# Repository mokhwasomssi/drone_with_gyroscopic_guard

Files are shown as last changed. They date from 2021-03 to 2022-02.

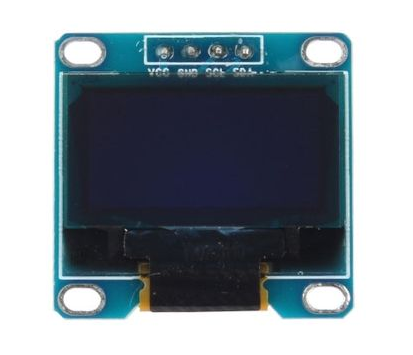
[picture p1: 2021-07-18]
reference/display/SSD1306 I2C Module 3.png

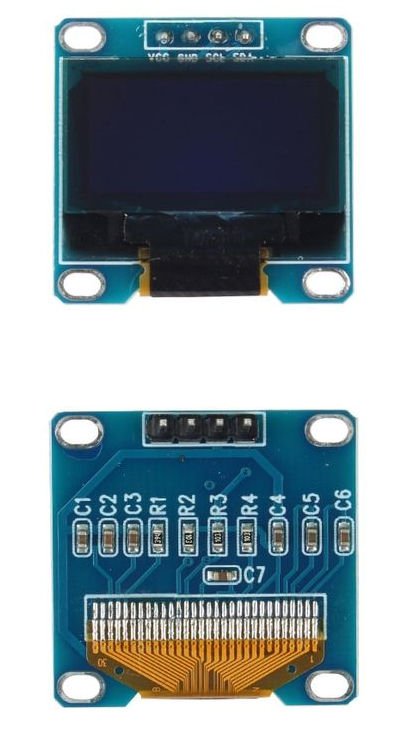
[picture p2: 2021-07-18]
reference/display/SSD1306 I2C Module 1.png

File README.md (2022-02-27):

# drone with gyroscopic guard

**Develop drone firmware and Design gyroscopic guard**



---

## Dev Environment
### Tools
- STM32CubeIDE
- Solidworks
- Kicad
 
---
## System Architecture

drone with my controller

---

## Parts

### 1. Gyroscopic Guard



#### Configuration

- 3mm carbon rod
- 3mm carbon plate
- Small bearing
- Shaft
- 3d printed parts

#### Feature

- Protect drones and Respond flexibly to collisions.
- x-axis drone mounter
- x-axis gyroscope ring
- y-axis gyroscope ring
- z-axis 2V geodesic sphere

### 2. Quadcopter



#### Configuration

- STM32F4CEU6 core board
- 210mm frame  
- 2207 2450KV BLDC  
- 5045 props  
- 3S-4S PDB  
- BLHeli_32 35A ESC  
- IMU (ICM20948)
- RF Transceiver (nrf24l01+pa+lna)
- Buzzer  
- 4S Lipo Battery  
- Battery Monitor Circuit
- SWD (st-link)  

#### Schematic



#### Feature

- 1 Khz PID loop
- Battery Monitor
- [ICM20948 library](https://github.com/mokhwasomssi/stm32_hal_icm20948.git)
- [Dshot protocol library](https://github.com/mokhwasomssi/stm32_hal_dshot.git)

### 3. Controller



#### Configuration

- STM32F4CEU6 core board
- Joy Stick X 2
- OLED LCD
- RF Transceiver (nrf24l01+pa+lna)
- Switch X 2 (with led)
- Buzzer
- 18650 battery X 2

#### Schematic


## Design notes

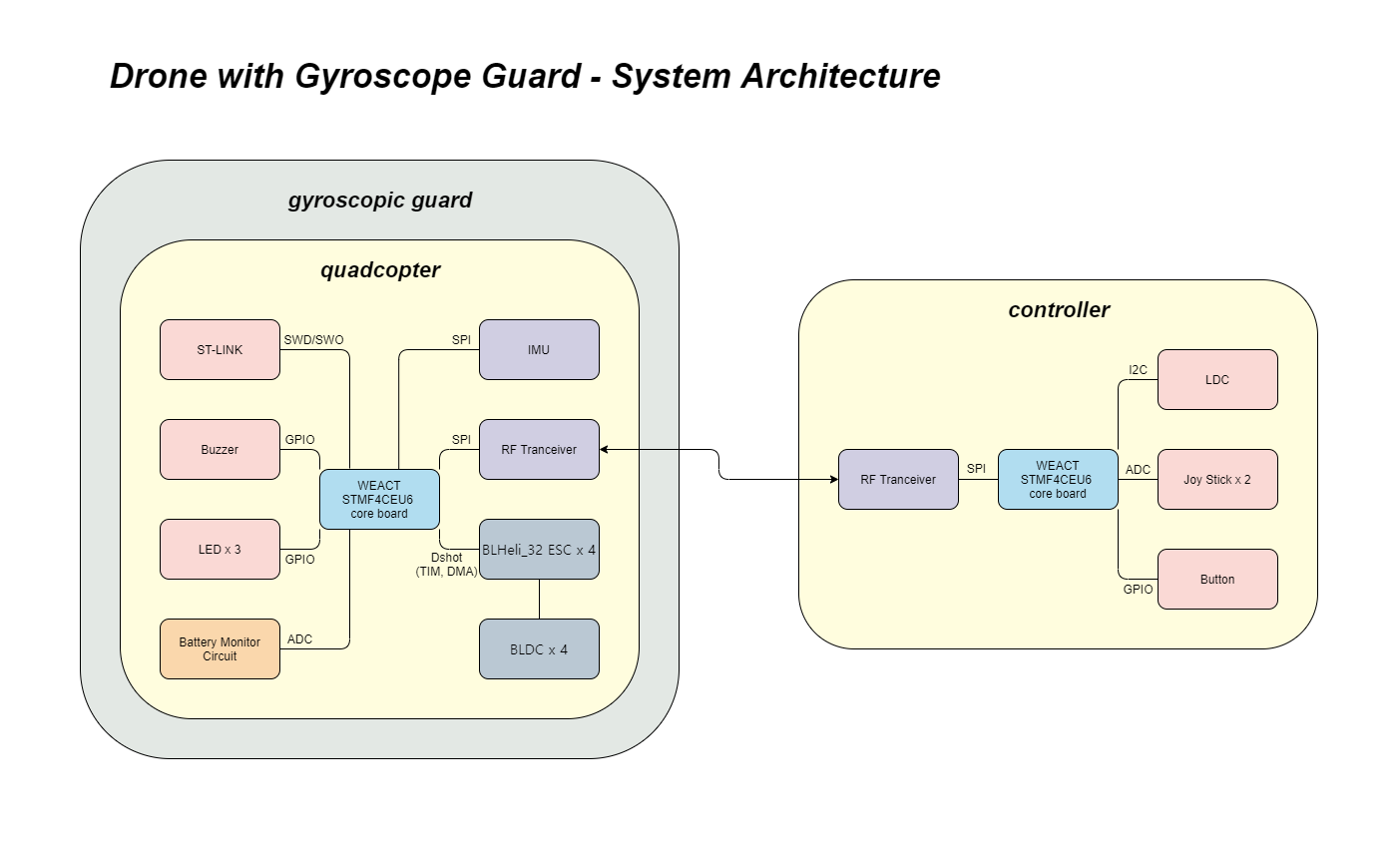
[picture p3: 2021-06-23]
docs/System Architecture.png

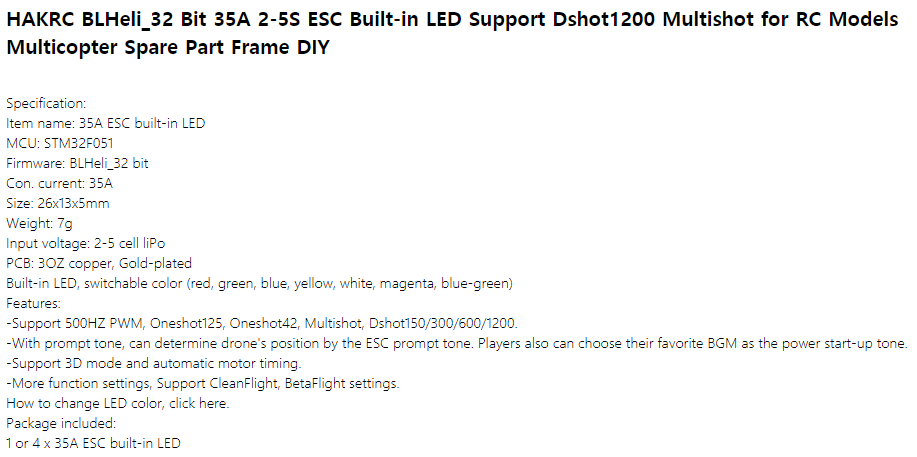
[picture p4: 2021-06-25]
reference/esc/HAKRC BLHeli_32 35A ESC Spec.png

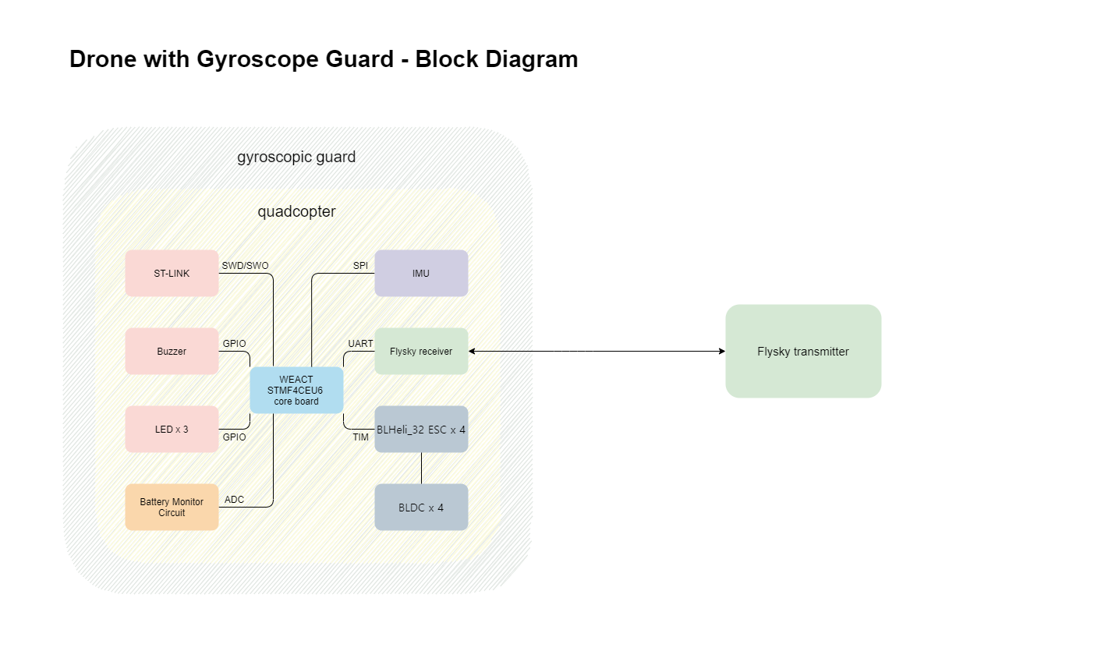
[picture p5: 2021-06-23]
docs/drone with flysky controller.png

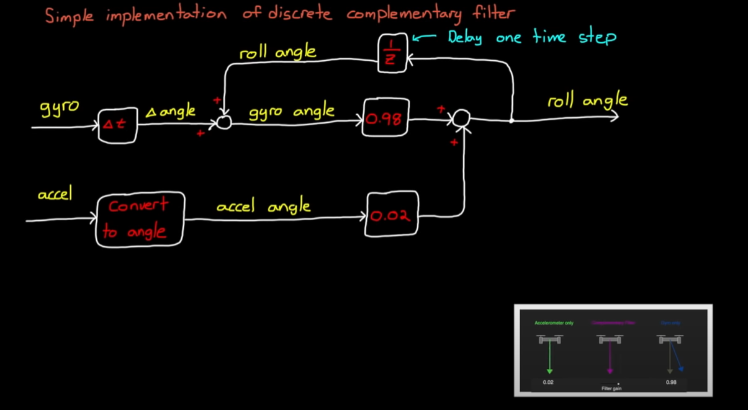
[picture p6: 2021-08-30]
document/complementary filter.png

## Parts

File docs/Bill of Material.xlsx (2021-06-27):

quadcopter |  |  | controller
 | 품명 | 구매처
1 | WeAct Black Pill V3.0 (STM32F411CEU6) |  | 1 | WeAct Black Pill V3.0 (STM32F411CEU6)
2 | SparkFun 9Dof IMU Breakout - ICM-20948 (Qwiic) |  | 2 | nrf24l01+pa+lna rf transceiver module
3 | nrf24l01+pa+lna rf transceiver module |  | 3 | SSD1306 OLED 128x64 0.96inch I2C
4 | Matek PDB-XT60 3-4S |  | 4 | joystick |  | 14.8 | 16.8 | diff
5 | HAKRC BLHeli_32 Bit 35A 2-5S ESC |  | 5 |  | 1 | 14.8 | 16.8 | 2
6 | lm358n |  | 6 |  | 2 | 7.4 | 8.4 | 1
7 | ZOP Power 14.8V 1800mAh 65C 4S Lipo Battery XT60 Plug | 뱅굿 (https://www.banggood.com/ZOP-Power-14_8V-1800mAh-65C-4S-Lipo-Battery-XT60-Plug-For-RC-FPV-Racing-Drone-p-1089557.html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) | 7 |  | 3 | 4.933333333 | 5.6 | 0.6666666667
8 | iFlight XING E 2207 2450KV |  | 8 |  | 4 | 3.7 | 4.2 | 0.5
9 |  |  | 9 |  | 5 | 2.96 | 3.36 | 0.4
 |  |  | 10 |  | 6 | 2.466666667 | 2.8 | 0.3333333333
 |  |  | 11 |  | 7 | 2.114285714 | 2.4 | 0.2857142857
 |  |  | 12 |  | 8 | 1.85 | 2.1 | 0.25
 |  |  |  |  | 9 | 1.644444444 | 1.866666667 | 0.2222222222
 |  |  |  |  | 10 | 1.48 | 1.68 | 0.2

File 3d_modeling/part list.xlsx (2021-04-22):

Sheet: Sheet1
axis | inner diameter | gap | outter diameter | gimbal interval
0 | - | - | 340
1 | 380 | 20 | 400 | 40
2 | 420 | 30 | 440 | 20
3 | 460 | 30 | 450 | 20
 | unit | mm
 | thickness | 4mm
 | shaft diameter | 3mm | shaft length | 22.5mm
hub | num |  | M3
5 | 12 |  | 32 pairs | depth
6_1 | 20 |  | 8*4 | more than 15mm
6_2 | 10

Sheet: 2021-03-31
gyroscope-drone
main-assembly | sub-assembly |  | part
name | no. | name | no. | name | description | weight (g) | quantity
gyro-drone | 1 | drone | 1 | 5045 CW/CCW props |  | 468 | 2
 |  |  | 2 | 2207 motor |  |  | 4 |  | finished product
 |  |  | 3 | 210mm frame |  |  | 1 | 468
 | 2 | gimbal | 1 | gimbal 0 | 340*40 | 36 | 1 | 36 | 3d printed model
 |  |  | 2 | gimbal 1 | inner Φ380, outer Φ400 | 10 | 8 | 80
 |  |  | 3 | gimbal 2 | inner Φ420, outer Φ440 |  | 8 | 0 | carbon fiber
 |  |  | 4 | connector0 |  | 12 | 4 | 48
 |  |  | 5 | connector1 | no hole | 4 | 8 | 32 | 3d printer
 |  |  | 6 | connector1_roll |  | 4 | 4 | 16 | sindoh(신도리코) DP102(DP200)
 |  |  | 7 | connector1_pitch |  | 4 | 4 | 16
 |  |  | 8 | connector2 | no hole |  | 8 | 0
 |  |  | 9 | connector2_pitch |  |  | 4 | 0 |  | 112
 |  |  | 10 | connector2_yaw |  |  | 4 | 0
 |  |  | 11 | shaft | Φ4*20 | 12 | 6 | 12
 |  |  | 12 | bearing | L-740ZZ | 0 | 12
 | 3 | sphere (d = 480) | 1 | carbon rod A type | Φ3*140.33 | 91 | 60 | 91
 |  |  | 2 | carbon rod B type | Φ3*123.17 | 80 | 60 | 80
 |  |  | 3 | 5hub |  |  | 10
 |  |  | 4 | 5hub-axis-bottom | yaw axis |  | 2
 |  |  | 5 | 5hub-axis-top |  |  | 2
 |  |  | 6 | 6hub |  |  | 20
 |  |  | 7 | 6hub-hemisphere | hemisphere |  | 10
 |  |  |  |  |  |  |  | 879 | 무게 1kg 이내로

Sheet: 2021-04-01
main-assembly | sub-assembly |  | part
name | no. | name | no. | name | size (mm) | weight (g) | quantity
gyro-drone | 1 | drone | 1 | 5045 CW/CCW props |  | 468 | 2
 |  |  | 2 | 2207 motor |  |  | 4 |  | finished product
 |  |  | 3 | 210mm frame |  |  | 1 |  |  | 3d printer
 | 2 | mount | 1 | [mount] frame | 340*40 | 36 | 1 |  | 3d print | sindoh(신도리코) DP102(DP200)
 |  |  | 2 | [mount] bracket |  |  | 4
 |  |  | 3 | bearing | inner Φ4, outer Φ7, width 2.5 |  | 4 |  | carbon fiber
 | 3 | roll-ring (inner Φ380, outer Φ400) | 1 | [roll-ring] frame | inner Φ380, outer Φ400, thickness 10 | 10 | 8
 |  |  | 2 | [roll-ring] bracket-basic |  |  | 8 |  | 베어링 폭 2.6으로
 |  |  | 3 | [roll-ring] bracket-roll | hole Φ3.2, bearing width 2.6 |  | 4 |  | 브라켓 홀 3.2로
 |  |  | 4 | [roll-ring] bracket-pitch | hole Φ3.2, bearing width 2.6 | 12 | 4 |  | bearing width 2.6
 |  |  | 5 | shaft | Φ4*25 | 12 | 2
 |  |  | 6 | bearing | inner Φ4, outer Φ7, width 2.5 | 0 | 8
 | 4 | pitch-ring (inner Φ420, outer Φ440) | 1 | [pitch-ring] frame | inner Φ420, outer Φ440, thickness 10 |  | 8
 |  |  | 2 | [pitch-ring] bracket-basic |  |  | 8
 |  |  | 3 | [pitch-ring] bracket-pitch | hole Φ3.2, bearing width 2.6 |  | 4
 |  |  | 4 | [pitch-ring] bracket-yaw | hole Φ3.2, bearing width 2.6 |  | 4
 |  |  | 5 | shaft | Φ4*25 |  | 2
 |  |  | 6 | bearing | inner Φ4, outer Φ7, width 2.5 |  | 8
 | 5 | yaw-sphere (d = 480mm) | 1 | carbon rod A type | Φ3*140 | 91 | 60
 |  |  | 2 | carbon rod B type | Φ3*123 | 80 | 60
 |  |  | 3 | 5hub | hole Φ3.2 |  | 10 | 12
 |  |  | 4 | 5hub-yaw-1 | hole Φ3.2, yaw axis |  | 2
 |  |  | 5 | 5hub-yaw-2 |  |  | 2
 |  |  | 6 | 6hub | hole Φ3.2 |  | 20
 |  |  | 7 | 6hub-hemisphere | hole Φ3.2 |  | 10
 |  |  |  |  |  |  |  |  | 무게 1kg 이내로

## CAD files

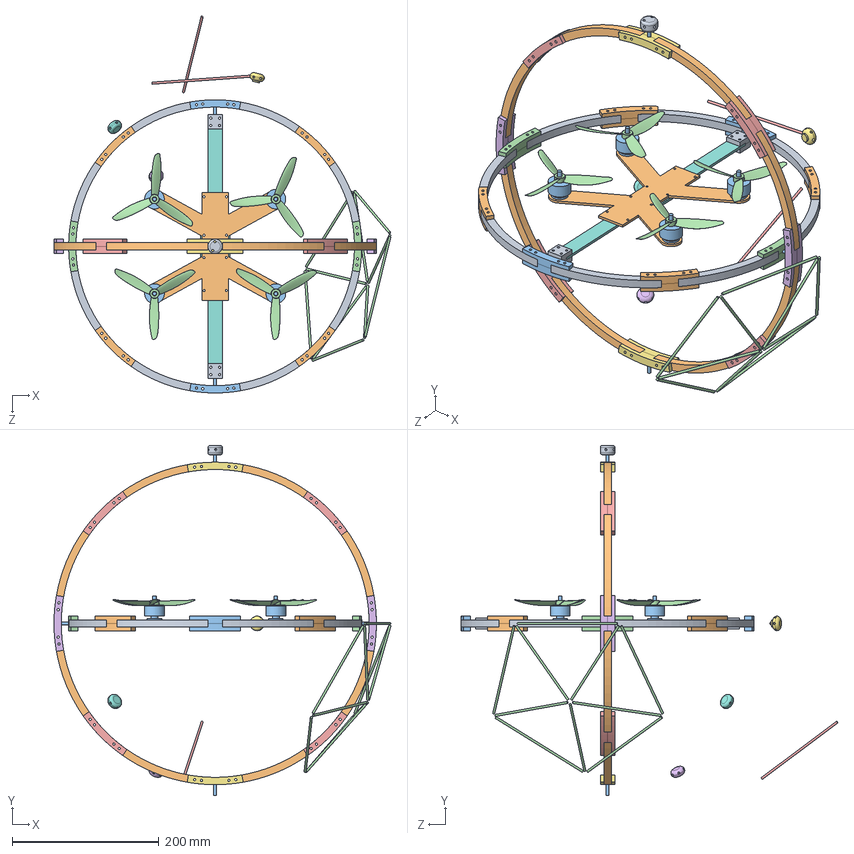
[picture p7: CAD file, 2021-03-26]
3d modeling/gyro-drone - assem.SLDASM
459.9 x 478.0 x 514.2 mm
connector0 x 4
connector1 x 8
connector1_roll x 4
connector1_pitch x 4
connector2 x 8
connector2_pitch x 4
connector2_yaw x 4
gimbal0
gimbal1 x 8
gimbal2 x 8
4x20 shaft x 6
QAV 210 - bottom plate
iFlight XING-E X2207 - motor x 4
5045 CCW.step x 4

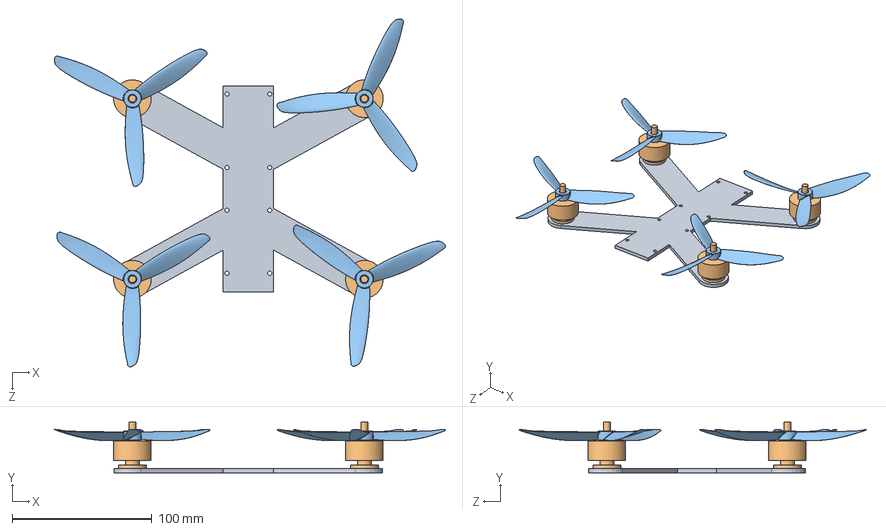
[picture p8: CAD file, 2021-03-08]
3d_modeling/1. drone/drone - assem.SLDASM
279.3 x 36.1 x 248.6 mm
QAV 210 - bottom plate
iFlight XING-E X2207 - motor x 4
5045 CCW.step x 4

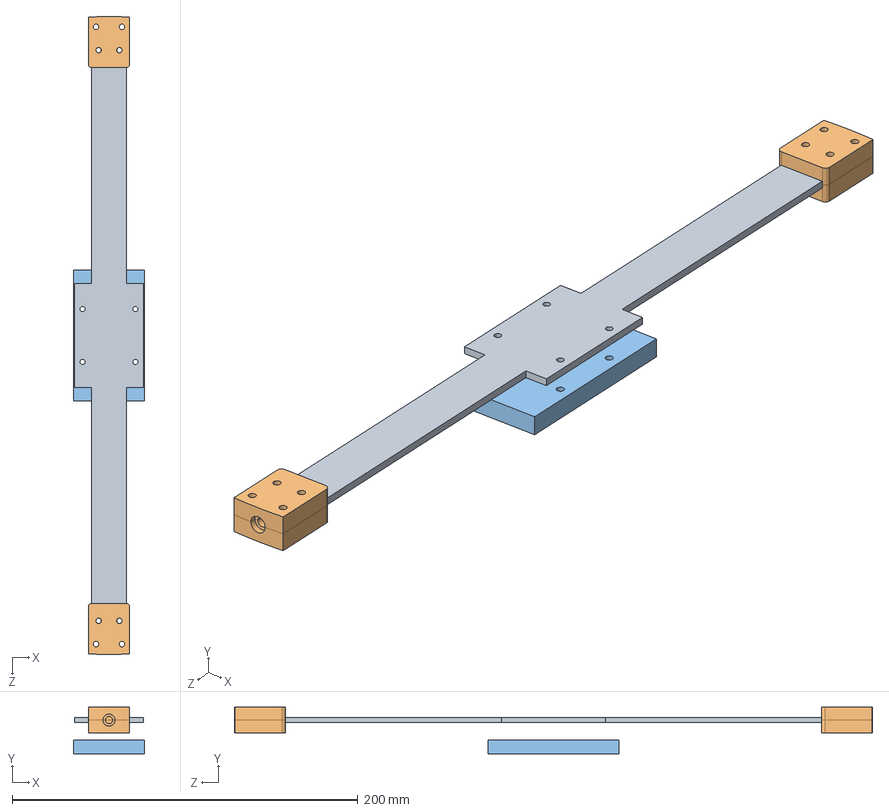
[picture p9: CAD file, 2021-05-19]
3d_modeling/2. mount/2. mount.SLDASM
41.0 x 27.0 x 369.0 mm
[mount] frame
[mount] bracket x 4
[mount] battery holder

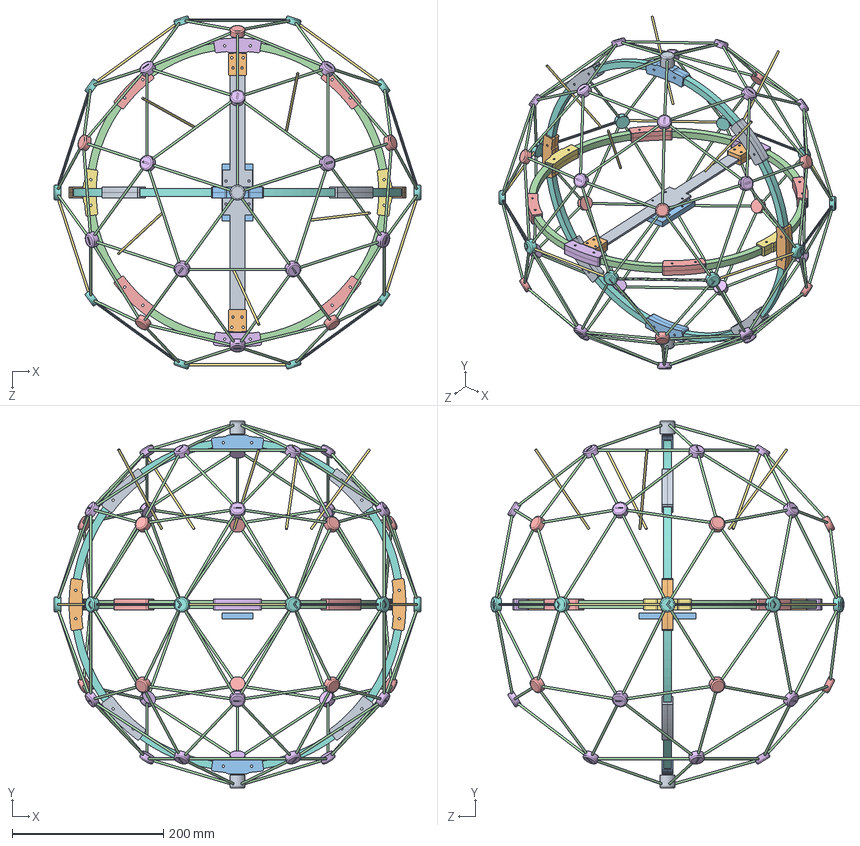
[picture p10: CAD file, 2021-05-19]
3d_modeling/drone with gyroscope guard.SLDASM
486.0 x 486.0 x 467.3 mm
[mount] frame
[mount] bracket x 4
[mount] battery holder
[roll-ring] frame x 8
[roll-ring] bracket-basic x 8
[roll-ring] bracket-roll x 4
[roll-ring] bracket-pitch x 4
[pitch-ring] frame x 8
[pitch-ring] bracket-basic x 8
[pitch-ring] bracket-pitch x 4
[pitch-ring] bracket-yaw x 4
pentagon x 12
5hub x 10
6hub x 20
3mm carbon rod x 5
6hub-hemisphere x 10
5hub-yaw-1 x 2
L-740ZZ - ball bearing x 8
4x25 shaft x 4

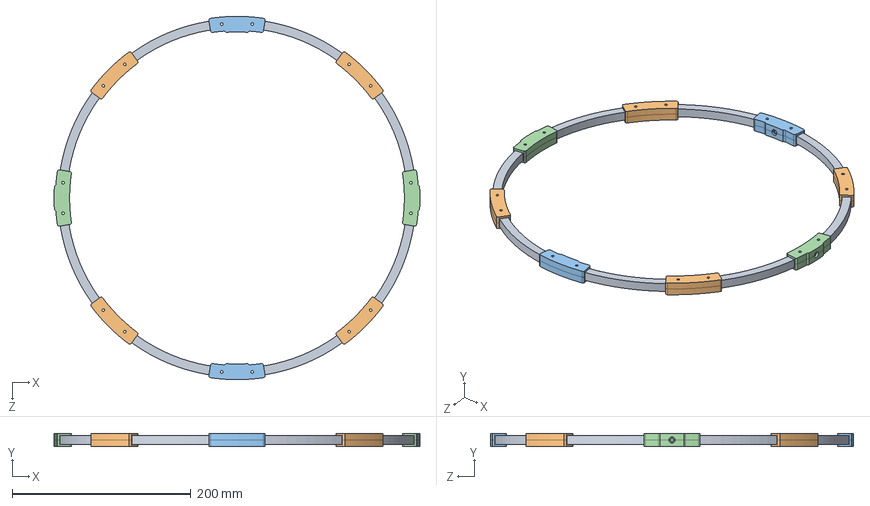
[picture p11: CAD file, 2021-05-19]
gyroscopic_guard_3d/3. roll-ring/3. roll-ring.SLDASM
409.0 x 15.0 x 406.0 mm
[roll-ring] frame x 8
[roll-ring] bracket-basic x 8
[roll-ring] bracket-roll x 4
[roll-ring] bracket-pitch x 4

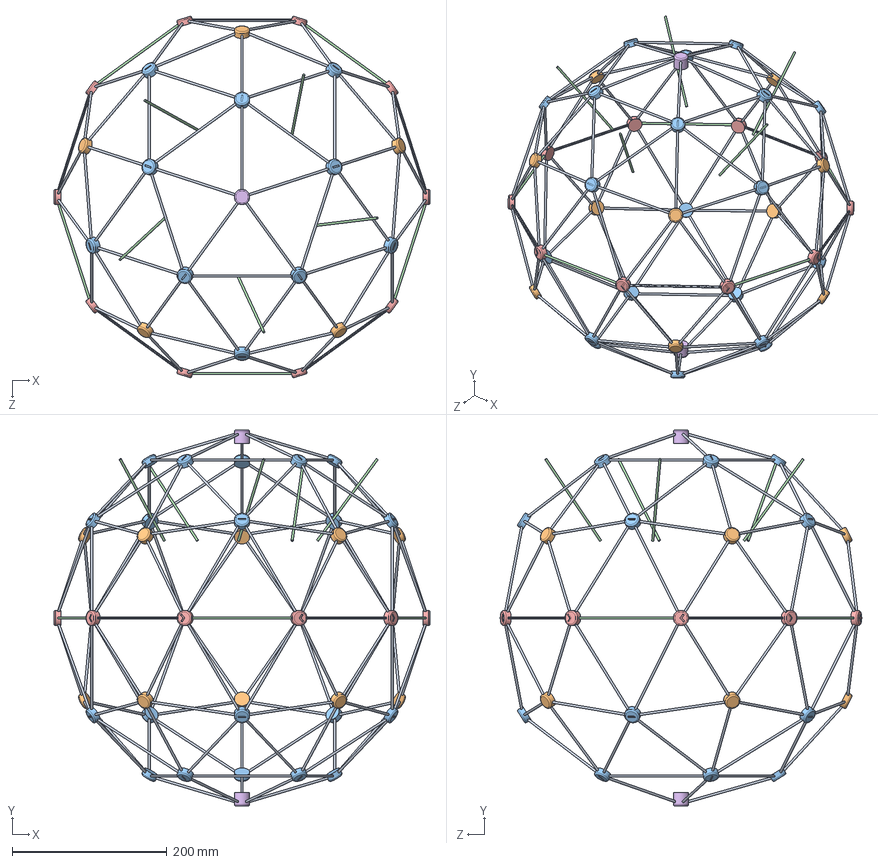
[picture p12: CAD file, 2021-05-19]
gyroscopic_guard_3d/5. yaw-sphere/5. yaw-sphere.SLDASM
486.0 x 486.0 x 467.3 mm
pentagon x 12
5hub x 10
6hub x 20
3mm carbon rod x 5
6hub-hemisphere x 10
5hub-yaw-1 x 2

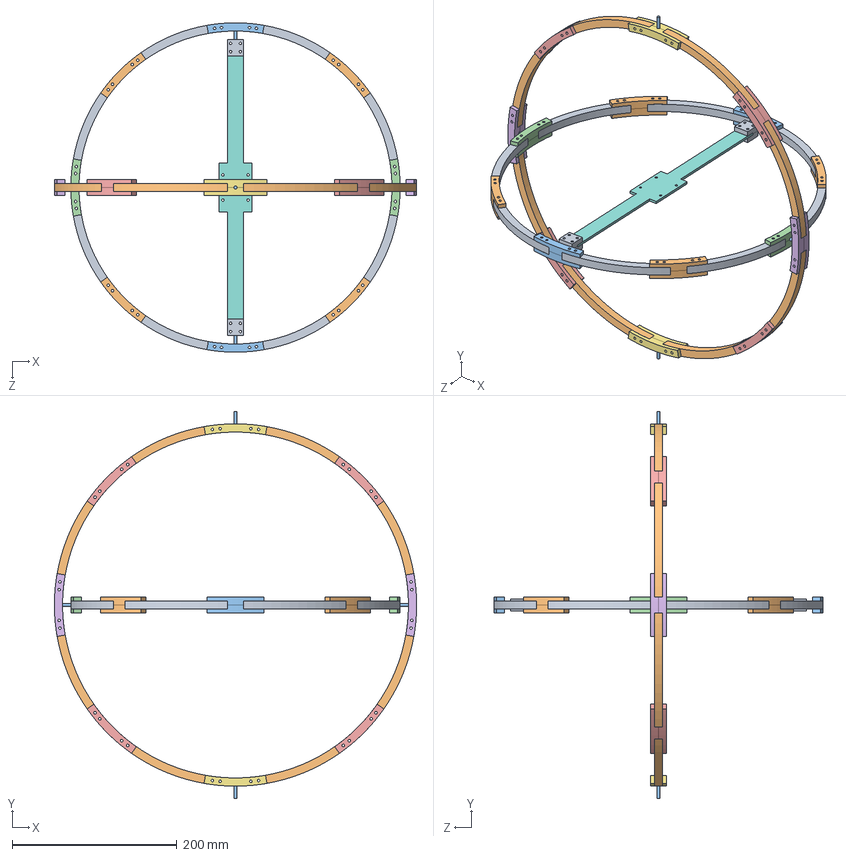
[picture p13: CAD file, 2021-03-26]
gyroscopic_guard_3d/etc/gimbal/gimbal - assem.SLDASM
439.9 x 470.0 x 399.9 mm
connector0 x 4
connector1 x 8
connector1_roll x 4
connector1_pitch x 4
connector2 x 8
connector2_pitch x 4
connector2_yaw x 4
gimbal0
gimbal1 x 8
gimbal2 x 8
4x20 shaft x 6

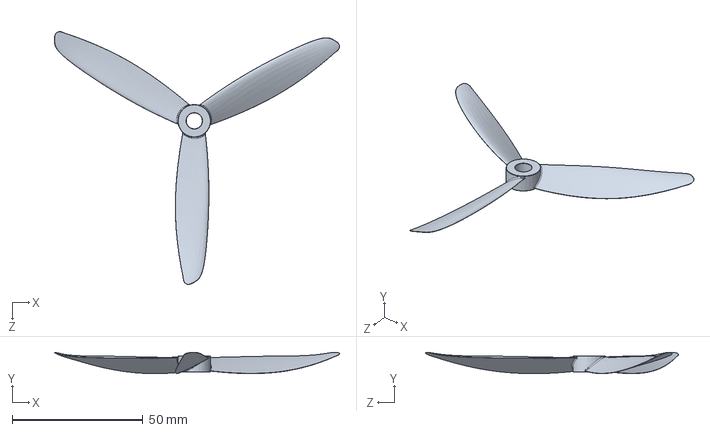
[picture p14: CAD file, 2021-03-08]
3d_modeling/1. drone/5045 CCW props.SLDASM
109.2 x 8.14 x 96.9 mm

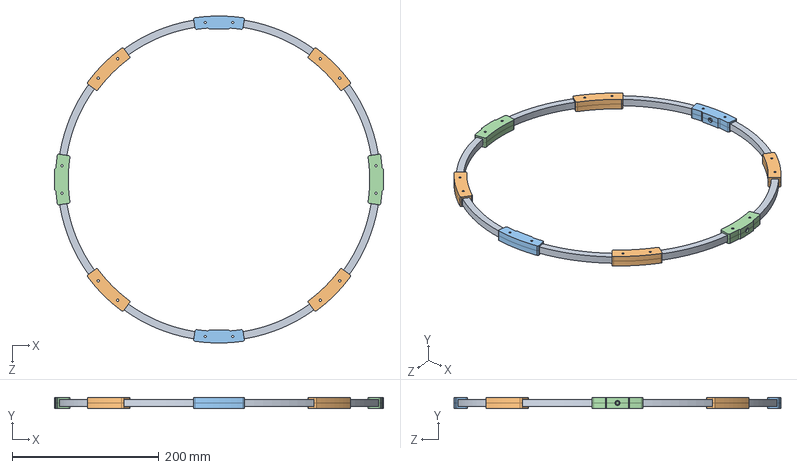
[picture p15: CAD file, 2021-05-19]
3d_modeling/4. pitch-ring/4. pitch-ring.SLDASM
449.0 x 15.0 x 446.0 mm
[pitch-ring] frame x 8
[pitch-ring] bracket-basic x 8
[pitch-ring] bracket-pitch x 4
[pitch-ring] bracket-yaw x 4

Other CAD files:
3d_modeling/etc/Tri-Blade 5045 Propeller.step.SLDASM
gyroscopic_guard_3d/1. drone/5045 CW props.SLDASM
gyroscopic_guard_3d/etc/Tri-Blade 5045 Propeller.step.SLDASM
3d modeling/1st, 2nd axis - gimbal/bearing holder - type 2.SLDPRT
3d_modeling/1. drone/5045 CW props.SLDASM
3d_modeling/1. drone/QAV 210 - bottom plate.SLDPRT
3d_modeling/1. drone/iFlight XING-E X2207 - motor.SLDPRT
3d_modeling/2. mount/[mount] battery holder.SLDPRT
3d_modeling/2. mount/[mount] bracket.SLDPRT
3d_modeling/2. mount/[mount] bracket.STL
3d_modeling/2. mount/[mount] frame.SLDPRT
3d_modeling/3. roll-ring/[roll-ring] bracket-basic.SLDPRT
3d_modeling/3. roll-ring/[roll-ring] bracket-basic.STL
3d_modeling/3. roll-ring/[roll-ring] bracket-pitch.SLDPRT
3d_modeling/3. roll-ring/[roll-ring] bracket-pitch.STL
3d_modeling/3. roll-ring/[roll-ring] bracket-roll.SLDPRT
3d_modeling/3. roll-ring/[roll-ring] bracket-roll.STL
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

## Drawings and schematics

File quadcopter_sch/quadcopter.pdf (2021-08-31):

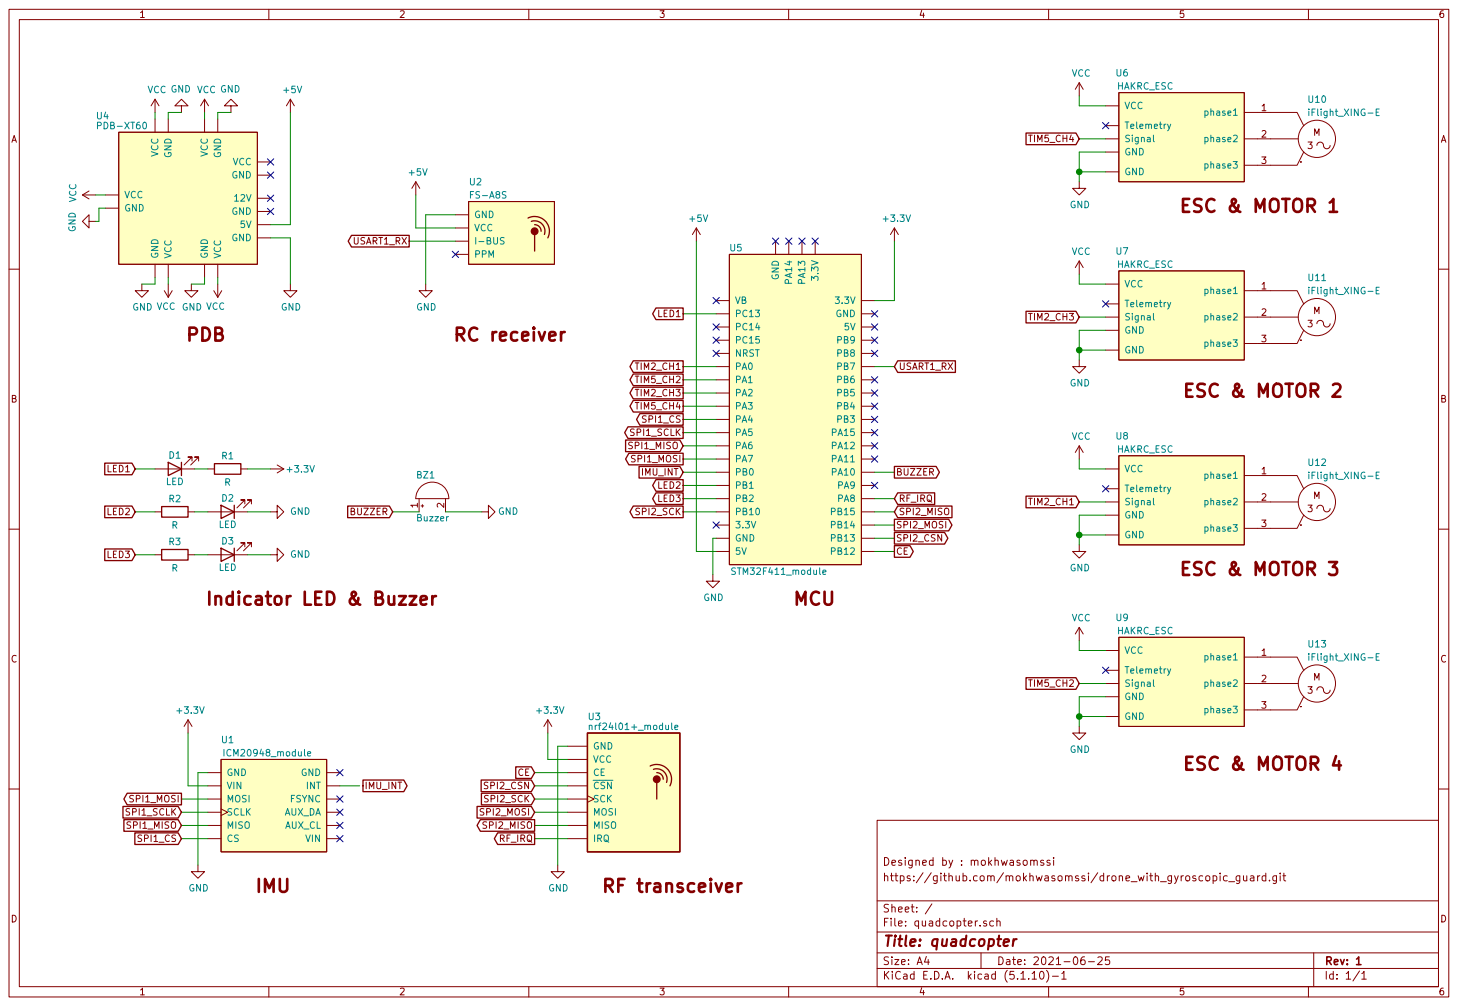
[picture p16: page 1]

CEGND
VCC
IRQ MISO MOSI SCK

INT MISO MOSI SCLK

File: quadcopter.sch Sheet: / https://github.com/mokhwasomssi/drone_with_gyroscopic_guard.git

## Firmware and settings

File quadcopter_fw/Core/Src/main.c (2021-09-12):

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
/* Includes ------------------------------------------------------------------*/
#include "main.h"
#include "dma.h"
#include "spi.h"
#include "tim.h"
#include "usart.h"
#include "gpio.h"

/* USER CODE BEGIN Includes */

/* standard library */
#include <stdio.h>
#include <math.h>
#include <stdbool.h>

/* private library */
#include "led.h"
#include "timer.h"
#include "interrupt.h"

#include "rc.h"
#include "imu.h"
#include "motor.h"
#include "telemetry.h"

/* USER CODE END Includes */


void SystemClock_Config(void);
/* USER CODE BEGIN 0 */

bool is_quadcopter_ready()
{
	rc_update(&my_rc_command);
	HAL_Delay(10);

	return my_rc_command.start;
}

uint16_t loop_time;

/* USER CODE END 0 */

/**
  * @brief  The application entry point.
  * @retval int
  */
int main(void)
{
  /* MCU Configuration--------------------------------------------------------*/

  /* Reset of all peripherals, Initializes the Flash interface and the Systick. */
  HAL_Init();

  /* Configure the system clock */
  SystemClock_Config();

  /* Initialize all configured peripherals */
  MX_GPIO_Init();
  MX_DMA_Init();
  MX_SPI1_Init();
  MX_TIM2_Init();
  MX_TIM5_Init();
  MX_TIM11_Init();
  MX_SPI2_Init();
  MX_USART1_UART_Init();
  MX_TIM10_Init();
  /* USER CODE BEGIN 2 */


  timer_init(); // timer for measuring operating time.
  rc_init();
  while(!is_quadcopter_ready());
  imu_init();
  motor_init();
  //telemetry_init();


  /* USER CODE END 2 */

  /* Infinite loop */
  /* USER CODE BEGIN WHILE */
  while (1)
  {
    /* USER CODE END WHILE */

    /* USER CODE BEGIN 3 */

	  if(imu_ready) // run control loop depending on imu sampling time
	  {				// ex) imu sampling time = 1.125khz, control loop cycle = 1.125khz
		timer1_start();

		led_green_on(); //control loop start

		rc_update();
		imu_update();
		motor_update();
		//telemetry_update();

		imu_ready = false;
		led_green_off(); //control loop end

		loop_time = timer2_end();
	  }

  }

  /* USER CODE END 3 */
}

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


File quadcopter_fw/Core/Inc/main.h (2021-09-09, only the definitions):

#define LED1_Pin GPIO_PIN_13
#define LED1_GPIO_Port GPIOC
#define MOTOR4_Pin GPIO_PIN_0
#define MOTOR4_GPIO_Port GPIOA
#define MOTOR3_Pin GPIO_PIN_1
#define MOTOR3_GPIO_Port GPIOA
#define MOTOR2_Pin GPIO_PIN_2
#define MOTOR2_GPIO_Port GPIOA
#define MOTOR1_Pin GPIO_PIN_3
#define MOTOR1_GPIO_Port GPIOA
#define SPI1_CS_Pin GPIO_PIN_4
#define SPI1_CS_GPIO_Port GPIOA
#define SPI1_SCK_Pin GPIO_PIN_5
#define SPI1_SCK_GPIO_Port GPIOA
#define SPI1_MISO_Pin GPIO_PIN_6
#define SPI1_MISO_GPIO_Port GPIOA
#define SPI1_MOSI_Pin GPIO_PIN_7
#define SPI1_MOSI_GPIO_Port GPIOA
#define IMU_IRQ_Pin GPIO_PIN_0
#define IMU_IRQ_GPIO_Port GPIOB
#define IMU_IRQ_EXTI_IRQn EXTI0_IRQn
#define LED2_Pin GPIO_PIN_1
#define LED2_GPIO_Port GPIOB
#define LED3_Pin GPIO_PIN_2
#define LED3_GPIO_Port GPIOB
#define SPI2_SCK_Pin GPIO_PIN_10
#define SPI2_SCK_GPIO_Port GPIOB
#define CE_Pin GPIO_PIN_12
#define CE_GPIO_Port GPIOB
#define SPI2_CSN_Pin GPIO_PIN_13
#define SPI2_CSN_GPIO_Port GPIOB
#define SPI2_MISO_Pin GPIO_PIN_14
#define SPI2_MISO_GPIO_Port GPIOB
#define SPI2_MOSI_Pin GPIO_PIN_15
#define SPI2_MOSI_GPIO_Port GPIOB
#define IRQ_Pin GPIO_PIN_8
#define IRQ_GPIO_Port GPIOA
#define IRQ_EXTI_IRQn EXTI9_5_IRQn
#define BUZZER_Pin GPIO_PIN_10
#define BUZZER_GPIO_Port GPIOA

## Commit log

2021-02-18 Import dshot.h/.c and Fix the situation that only two motor, not four was spinning
    [main.c, main.h]
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2021-02-28 Fix ibus update problem
    [main.c, main.h]
2021-03-01 Add arming/disarming and fail-safe
    [main.c]
2021-03-05 Add 3d modeling files
    [5045 3 blades - props.SLDPRT, Assem.SLDASM, QAV 210 - bottom plate.SLDPRT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]
2021-03-06 Add bearing holder in 3d modeling folder
    [Assem.SLDASM, KFL 08 - unit bearing.SLDPRT, L-630ZZ - ball bearing.SLDPRT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]
2021-03-06 Add 'gimbal with bearing holder - assem' file
    [3mm shaft.SLDPRT, L-630ZZ - ball bearing.SLDPRT, bearing holder - type 1.SLDPRT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]
2021-03-07 Add 5-way hub to sphere
    [2v geodesic sphere - 420mm diameter.SLDPRT, 2v geodesic sphere - 427.8 diameter.SLDPRT, 2v geodesic sphere - assem.SLDASM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]
2021-03-08 Complete 3d modeling
    [2v geodesic sphere - 420mm diameter.SLDPRT, 2v geodesic sphere - 427.8 diameter.SLDPRT, 2v geodesic sphere - assem.SLDASM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]
2021-03-10 Update part list
    [bearing holder to gimbal base.SLDPRT, gimbal - assem.SLDASM, gyrodscope-drone - assem.SLDASM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]
2021-03-11 Make drawing files
    [3mm shaft.SLDPRT, 4mm shaft.SLDPRT, 5hub-axis.SLDPRT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]
2021-03-26 Modify design for 3d print output
    [4x20 shaft.SLDPRT, 4x25 shaft.SLDPRT, 5hub-axis-bottom.SLDPRT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]
2021-03-26 Modify design for 3d print output 2
    [5hub-axis-bottem.STL, 5hub-axis-bottom.SLDPRT, 5hub-axis-top.STL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]
2021-03-26 Update reference
    [3mm carbon rod.SLDPRT, 4x20 shaft.SLDPRT, 4x25 shaft.SLDPRT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]
2021-03-30 Start drawing schematic
    [schematic.kicad_pcb, schematic.sch]
2021-04-01 Modify 3d print design 3
    [part list.xlsx]
2021-04-01 Modify 3d print design 4
    [2. mount.SLDASM, 3. roll-ring.SLDASM, 4x25 shaft.SLDPRT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]
2021-04-05 Add quadcopter symbol
    [3. roll-ring.SLDASM, 5hub.SLDPRT, quadcopter.kicad_pcb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]
2021-04-06 Update quadcopter schematic
    [quadcopter.sch]
2021-04-06 Modify 3d print design 5
    [2. mount.SLDASM, 3. roll-ring.SLDASM, 4. pitch-ring.SLDASM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]
2021-04-09 Modify 3d print design 6
    [2. mount.SLDASM, 3. roll-ring.SLDASM, 3mm carbon rod.SLDPRT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]
2021-04-14 Update icm20948 library
    modify structure and function.
    [3mm carbon rod.SLDPRT, 4x20 shaft.SLDPRT, 4x25 shaft.SLDPRT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]
2021-04-17 Add voltage monitor
    - moving average filiter
    - voltage follower
    - error range : -0.6V ~ -0.3V
    [quadcopter.sch]
2021-04-17 Update voltage monitor
    - delete moving average filter
    [quadcopter.sch]
2021-04-17 Modify 3d print design 7
    [2. mount.SLDASM, 3. roll-ring.SLDASM, 4. pitch-ring.SLDASM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]
2021-04-19 Modify 3d print design 8
    - screw hole : 3.2mm
    - bearing mount hole width : 2.6mm
    [3. roll-ring.SLDASM, 4. pitch-ring.SLDASM, 5. yaw-sphere.SLDASM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]
2021-04-20 Add battery holder
    [2. mount.SLDASM, 3. roll-ring.SLDASM, [mount] battery holder.SLDPRT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]
2021-04-22 Add STL files
    - STL files of 3d modeling
    [2. mount.SLDASM, 4. pitch-ring.SLDASM, 5hub.STL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]
2021-05-06 Update FMU schematic
    [quadcopter.sch]
2021-05-08 Update FMU schematic
    - add 2 LED
    [quadcopter.sch]
2021-05-08 Add personal libraries in firmware/Lib
    - led.h/.c
    - buzzer.h/.c
    - battery_monitor.h/.c
    [firmware.ioc, main.c, main.h]
2021-05-12 Use SWO
    [firmware Debug.cfg]
2021-05-19 Modify 3d cad parts
    - narrow the gap between [roll-ring] bracket-roll and [pitch-ring] bracket-yaw
    - add shaft hole in 5hub-yaw
    [2. mount.SLDASM, 2v geodesic sphere - 420mm diameter.SLDPRT, 2v geodesic sphere - 427.8 diameter.SLDPRT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]
2021-05-19 Modify 3d cad part
    - battery holder
    [2. mount.SLDASM, 2v geodesic sphere - 420mm diameter.SLDPRT, 2v geodesic sphere - 427.8 diameter.SLDPRT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]
2021-06-23 Add controller_fw
    [firmware Debug.cfg]
2021-06-26 Update quadcopter schematic
    - redrawing for readability
    - add rf transceiver module
    - remove opamp used for battery monitoring
    [SSD1306 OLED 128x64 0.96inch I2C.sch, WeAct Black Pill V3.0 (STM32F411CEU6).sch, controller.kicad_pcb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]
2021-06-27 Add controller schematic
    [Bill of Material.xlsx, SSD1306 OLED 128x64 0.96inch I2C.sch, WeAct Black Pill V3.0 (STM32F411CEU6).sch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]
2021-06-27 Update controller schematic
    - add lcd module
    [2. mount.SLDASM, 2v geodesic sphere - 420mm diameter.SLDPRT, 2v geodesic sphere - 427.8 diameter.SLDPRT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]
2021-07-18 Display joystick value
    [quadcopter.sch]
2021-08-25 Update quadcopter schematic
    - add FS-A8S
    - rename symbals
    - relocation symbals in schematic
    [quadcopter.sch]
2021-08-25 Delete controller_fw and cotroller_sch
    - decide not to make controller
    - because the moving range of the joystick module is small
    [controller.sch]
2021-08-26 Apply all libraries at the same time
    - led & buzzer
    - icm20948
    - ibus
    - dshot
    - nrf24l01p
    [main.c, main.h, quadcopter_fw.ioc]
2021-08-26 Rename folders
    [2. mount.SLDASM, 2v geodesic sphere - 420mm diameter.SLDPRT, 2v geodesic sphere - 427.8 diameter.SLDPRT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]
2021-08-28 Add complementary filter
    - it works well
    - gyro drift is removed
    [firmware Debug.cfg]
2021-08-30 Use imu interrupt pin
    - estimate sensor update period using data ready interrupt
    [2. mount.SLDASM, 2v geodesic sphere - 420mm diameter.SLDPRT, 2v geodesic sphere - 427.8 diameter.SLDPRT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]
2021-08-30 Update quadcopter_fw
    - transmit current angle to computer
    [firmware Debug.cfg]
2021-08-31 Update quadcopter_fw
    - add rc_command.h/.c
    [2. mount.SLDASM, 2v geodesic sphere - 420mm diameter.SLDPRT, 2v geodesic sphere - 427.8 diameter.SLDPRT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]
2021-08-31 Update quadcopter_sck
    - add imu_int pin
    [quadcopter.sch]
2021-09-04 Update quadcopter_fw
    - add motor.h/.c
    [firmware Debug.cfg, pin_table.xlsx]
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

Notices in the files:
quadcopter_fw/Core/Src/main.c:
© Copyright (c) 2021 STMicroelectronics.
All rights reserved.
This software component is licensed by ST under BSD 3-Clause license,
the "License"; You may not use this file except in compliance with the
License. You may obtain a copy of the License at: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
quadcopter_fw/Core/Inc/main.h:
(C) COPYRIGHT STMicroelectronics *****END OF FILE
